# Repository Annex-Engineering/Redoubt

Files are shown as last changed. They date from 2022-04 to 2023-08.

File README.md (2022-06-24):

# Redoubt Printer

> :warning: **This project is still in beta**: Over many months the design has proven itself in the closed beta. However dedicated skirts for the z drives are still missing. Partial CAD is included to make any design as you wish.

Redoubt is entirely scratch design based on the efforts of the V2.2 for better performance, reliability and less maintenance. 

Our discord server can be found here: 

Join me on Discord (https://discord.gg/MzTR3zE)

BOM/Sourcing Guide can be found here: https://docs.google.com/spreadsheets/d/1O3eyVuQ6M4F03MJSDs4Z71_XyNjXL5HFTZr1jsaAtRc/edit?usp=sharing

# Project Goals:
- QuickDraw V2 probe
- Integrated Sherpa Mini
- Ultra compact and anti-backlash swivel z-joints
- Heavy duty XY and Z belt tensioning with one knob
- New CFD optimized part cooling ducts
- Reinforced XY joints
- Optimized for reduced belt wear
- Bearings with improved lifespan
- Quick-swap umbilical
- Carabiner support
- Reduced toolhead weight
- MGN12H support

Note: Enclosed Printers are passively heated and only designed around a 65C max chamber temperature, Redoubt is not intended to be a High Temperature printer. It was designed to excell at common engineering materials such as PLA, PETG, ABS and some PC/Nylon Blends

# Images
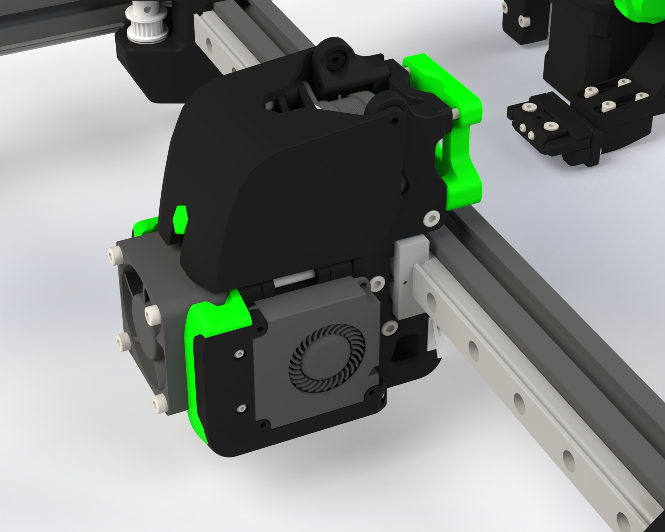
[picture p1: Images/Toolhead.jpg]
Image of Redoubt
 
  
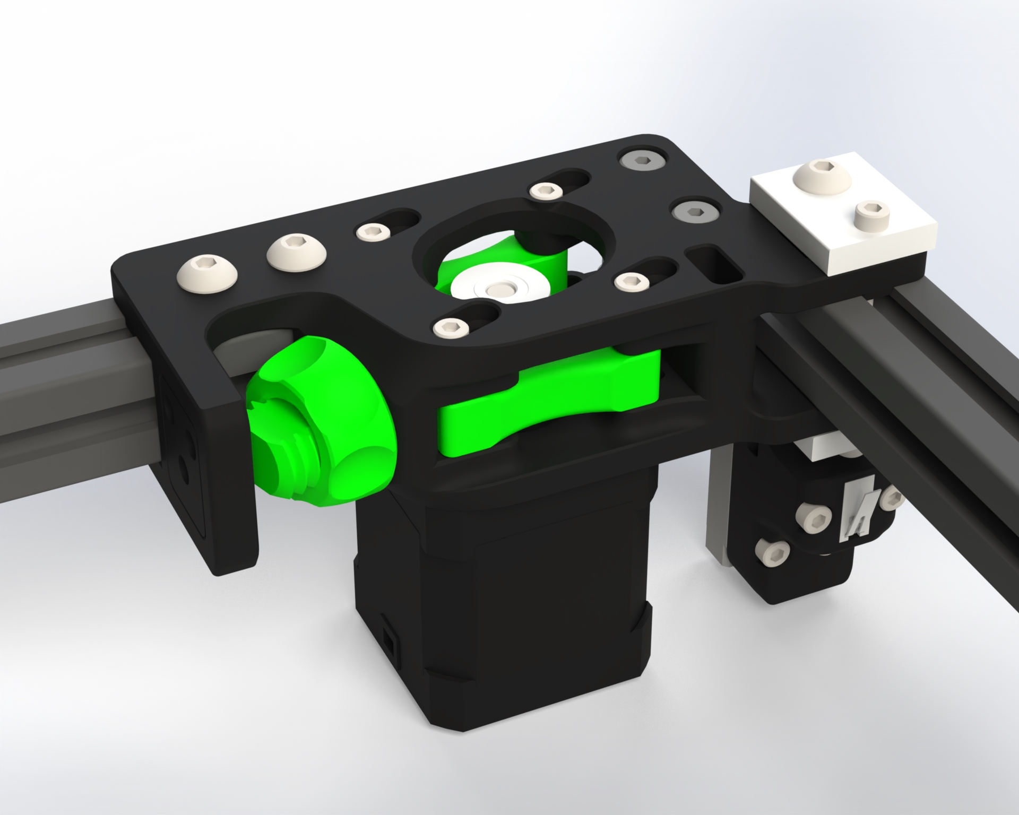
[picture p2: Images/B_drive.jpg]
Image of Redoubt
  

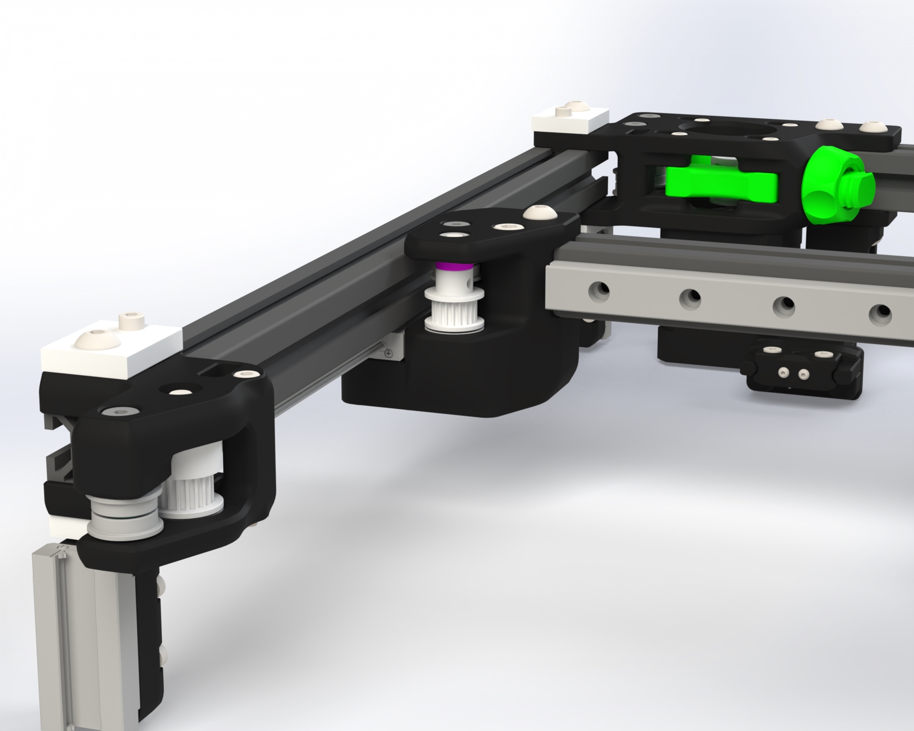
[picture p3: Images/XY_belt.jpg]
Image of Redoubt
 

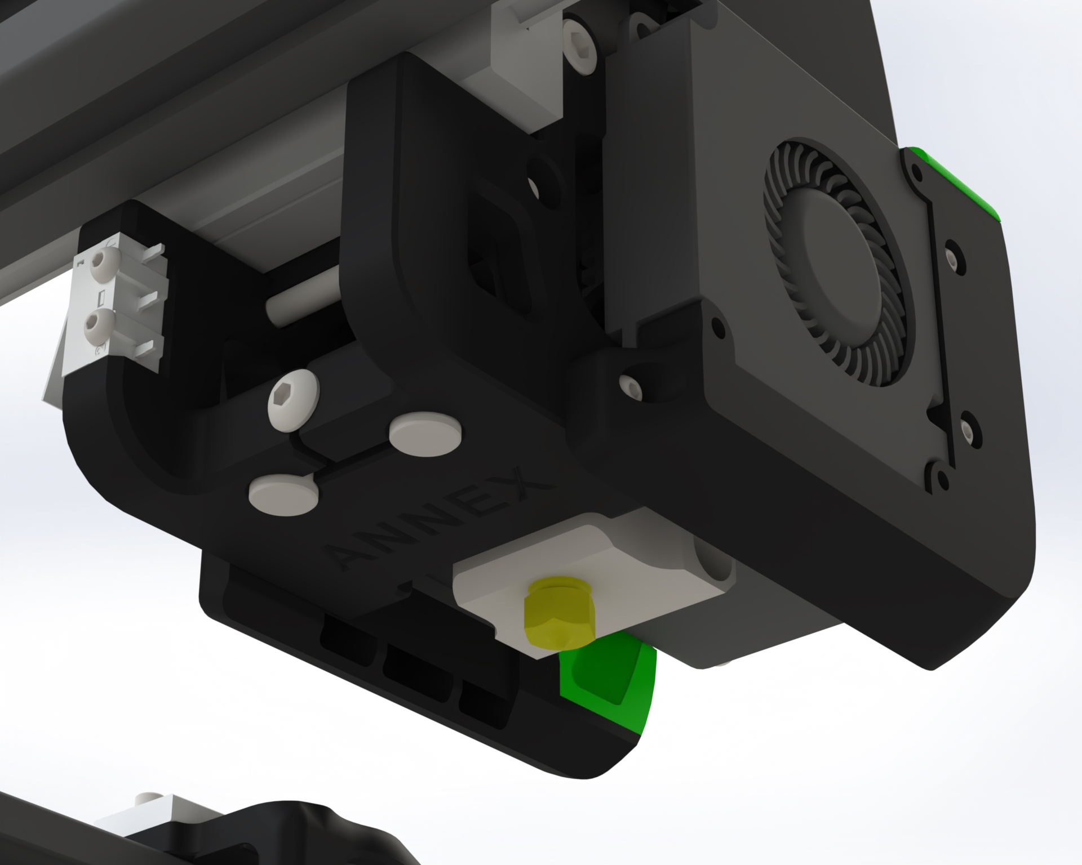
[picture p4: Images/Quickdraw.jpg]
Image of Redoubt
  
 
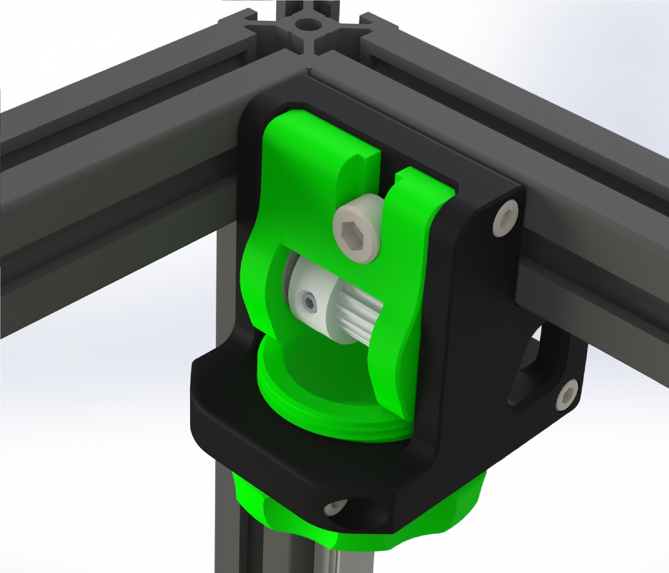
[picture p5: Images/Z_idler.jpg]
Image of Redoubt


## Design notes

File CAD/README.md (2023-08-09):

# Redoubt Printer

The CAD is from the Redoubt_Alpha_Mosquito_25_4_2022.EASM eDrawing with the worm z drives. You are welcome to make any necessary adaptations for different hotends and skirt designs according to your preferences. We would greatly appreciate your feedback and visual contributions on the Annex discord platform.

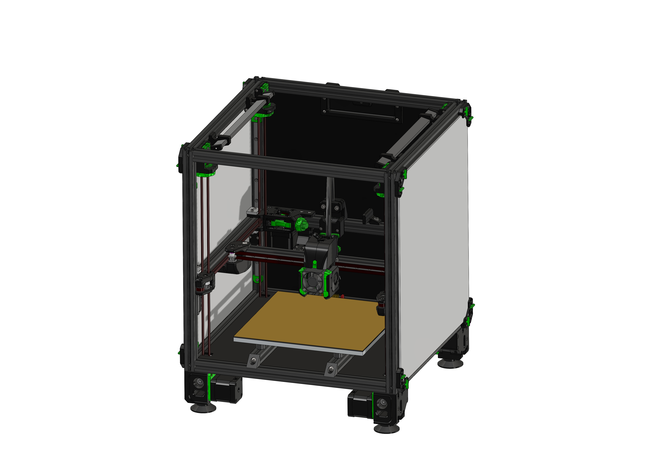
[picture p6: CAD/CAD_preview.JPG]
Image of Redoubt


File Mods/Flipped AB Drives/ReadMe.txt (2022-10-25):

This mod flips the motors on the AB drives so that they face upwards. This is important it you are running a flipped z configuration as it will prevent collisions between your steppers and the z idlers.

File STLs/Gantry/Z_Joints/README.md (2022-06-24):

# Compact swivel z joints

The Y-endstop is now hidden inside one of the z joints. This gives the gantry a cleaner look. Wiring goes behind the nema17 to the z chain. The spacer got new fins that will avoid botteming out the M10 screw and cracking the plastic.

Use 2 M2 self tappers to lock the switch in place. Start with the left side to avoid tilting. The switch can be removed by pushing a small key through the hole on the back.

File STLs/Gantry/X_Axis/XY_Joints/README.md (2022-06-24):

# XY Joints 

No more tall shimstacks are needed. The layout has been optimized for part strength and overtravel in the best way possible. Internal channels are used to reinforce the design. Use locknuts for additional security.

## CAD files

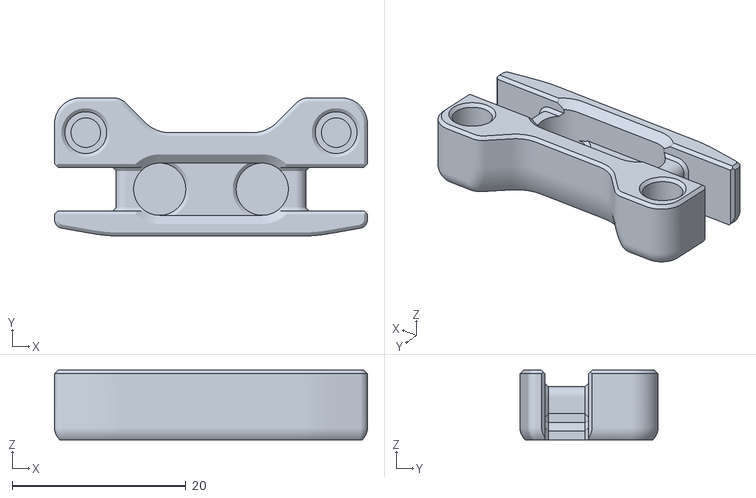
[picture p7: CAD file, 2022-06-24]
STLs/Gantry/QuickDraw V2/Dock_main_x1_Rev3.STL
36.0 x 15.9 x 8.00

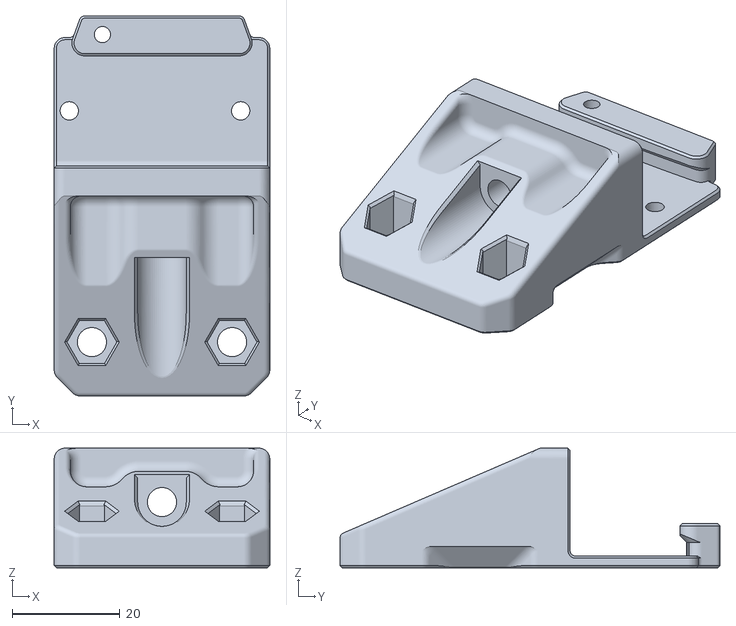
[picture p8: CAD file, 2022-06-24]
STLs/Gantry/Wiring/Cable_clamp_Carabiner_main_x1_Rev1.STL
40.0 x 70.5 x 22.2

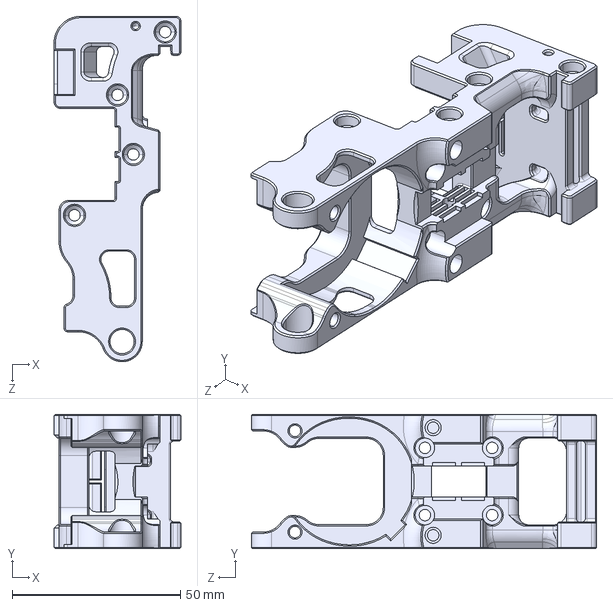
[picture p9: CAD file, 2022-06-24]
CAD/X_carriage.STEP
37.8 x 40.0 x 102.7 mm

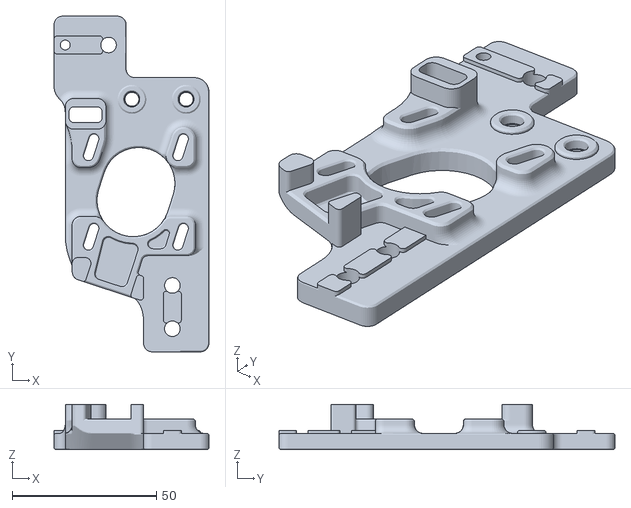
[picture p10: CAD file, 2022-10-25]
Mods/Flipped AB Drives/AB_Drive_bottem_L_Rev8_Flipped.STL
53.7 x 116.3 x 15.6

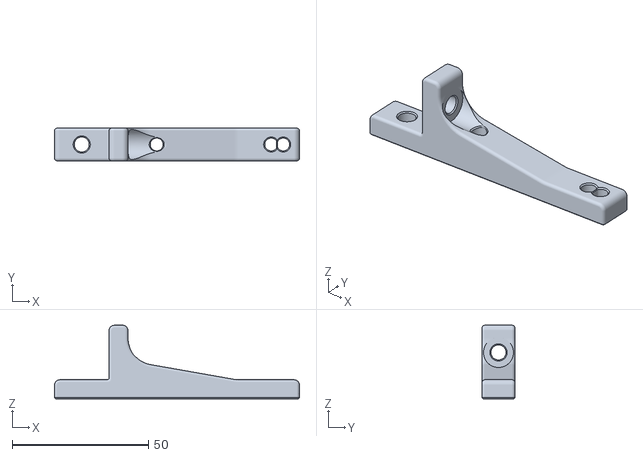
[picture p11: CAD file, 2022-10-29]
STLs/Electronics_Compartment/universal_meanwell_uhp_psu_mounting_bracket_x2_rev2.STL
89.9 x 12.0 x 27.0

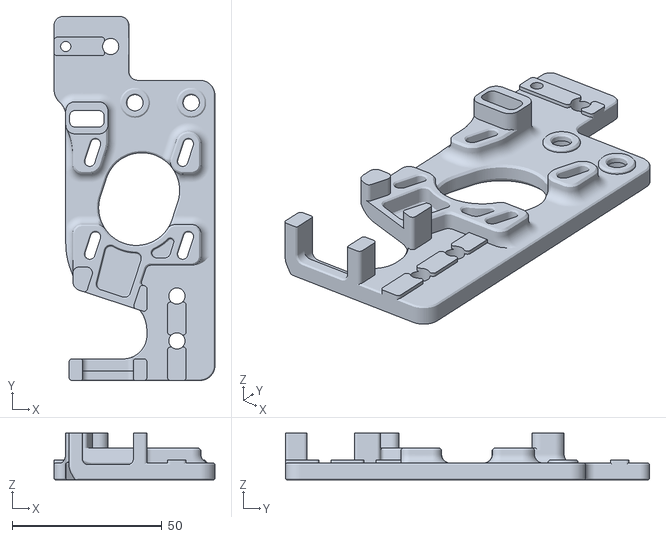
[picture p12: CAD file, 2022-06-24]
STLs/Gantry/AB_Drive_Units/B_Drive_top_ISO7379_x1_Rev4.STL
53.7 x 121.5 x 15.6

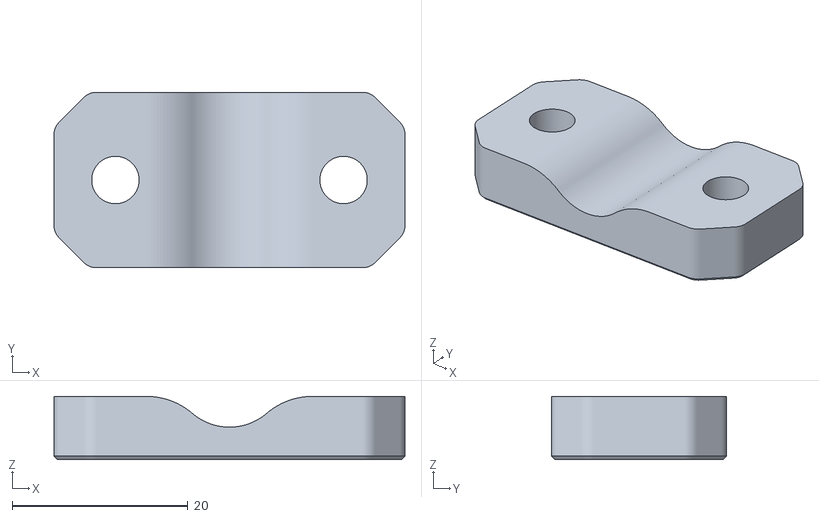
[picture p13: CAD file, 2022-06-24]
STLs/Gantry/Wiring/Cable_clamp_Carabiner_rear_x1_Rev1.STL
40.0 x 20.0 x 7.20

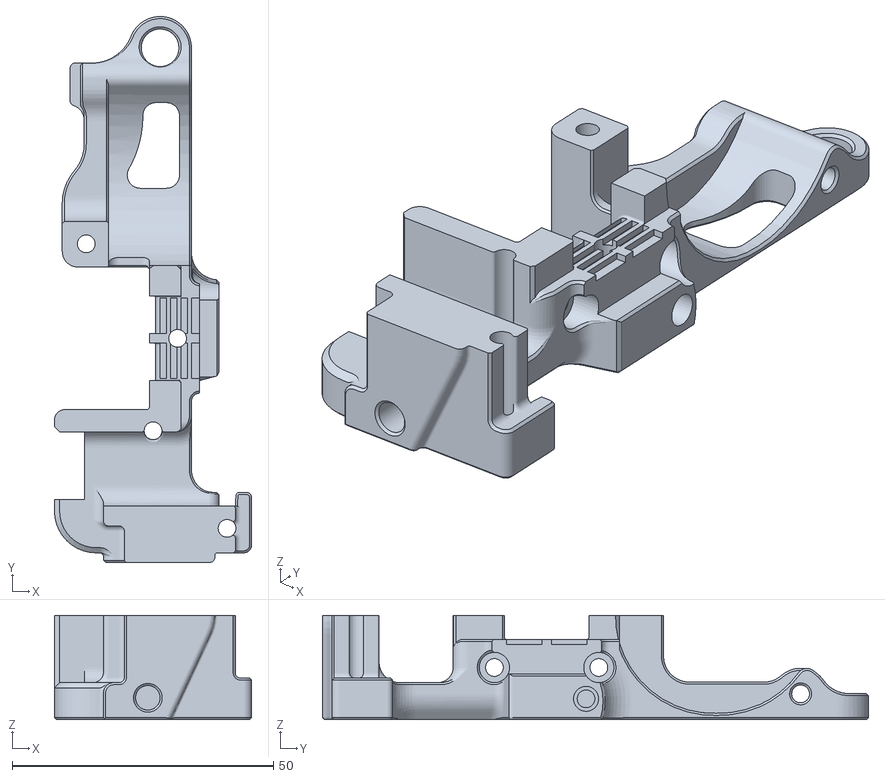
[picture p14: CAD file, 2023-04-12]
STLs/Gantry/X_Axis/X_Carriage/Beacon Carriage/X_carriage_R_Beacon_x1_Rev4.STL
37.8 x 104.6 x 20.0

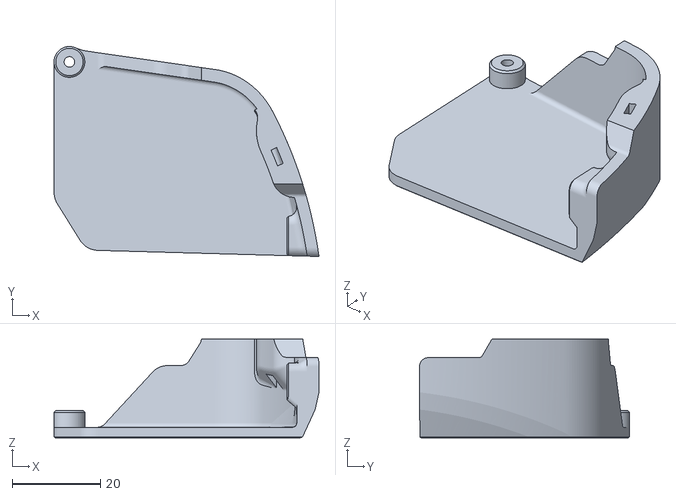
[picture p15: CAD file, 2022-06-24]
STLs/Gantry/X_Axis/X_Carriage/Toolhead_door_right_Rev2_x1.STL
60.1 x 47.6 x 22.4

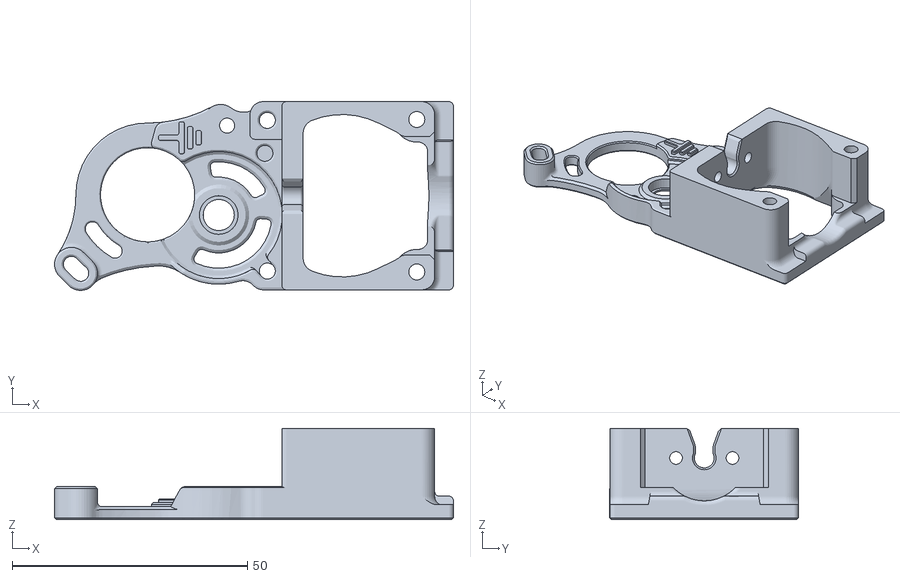
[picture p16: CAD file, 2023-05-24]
STLs/Gantry/X_Axis/X_Carriage/Toolheads/Hotends/Mosquito_hotend_mount_rear_Rev3.STL
84.8 x 40.1 x 19.4

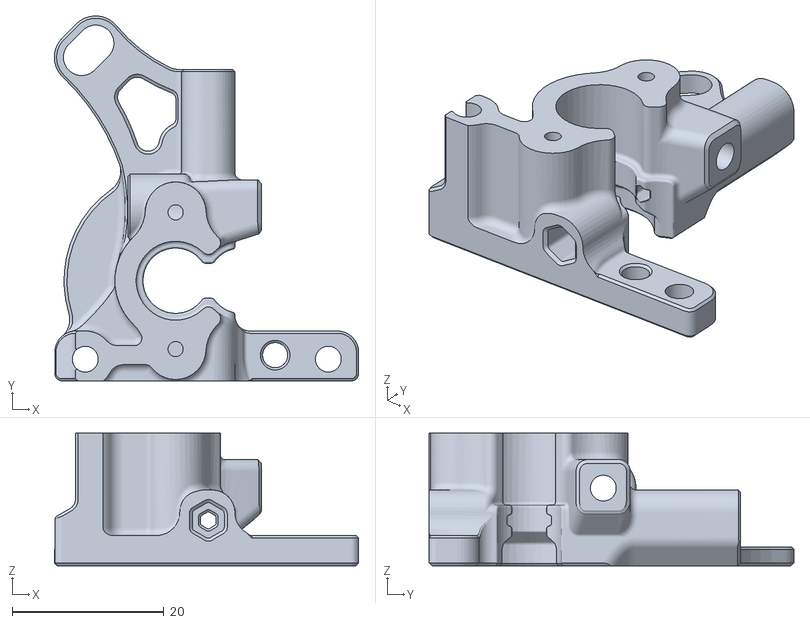
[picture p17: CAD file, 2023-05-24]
STLs/Gantry/X_Axis/X_Carriage/Toolheads/Sherpa_mini_core_x1_rev2.STL
40.1 x 48.0 x 17.5

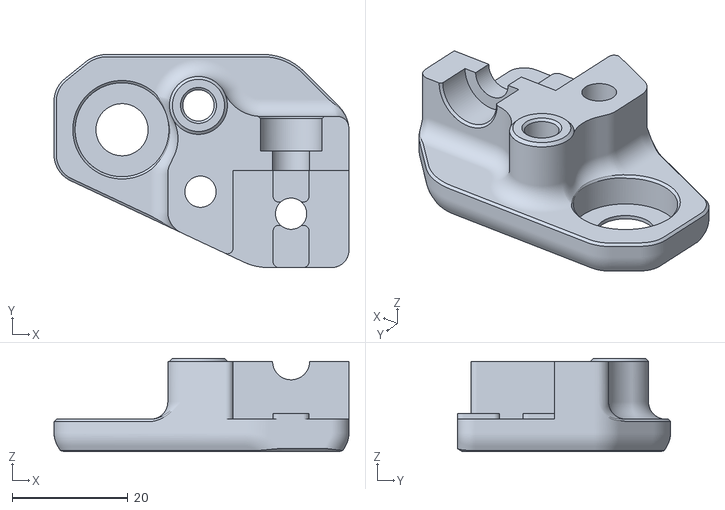
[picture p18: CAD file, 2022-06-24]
STLs/Gantry/X_Axis/XY_Joints/XY_joint_R_top_ISO7979_x1_Rev4.STL
50.9 x 36.8 x 16.1

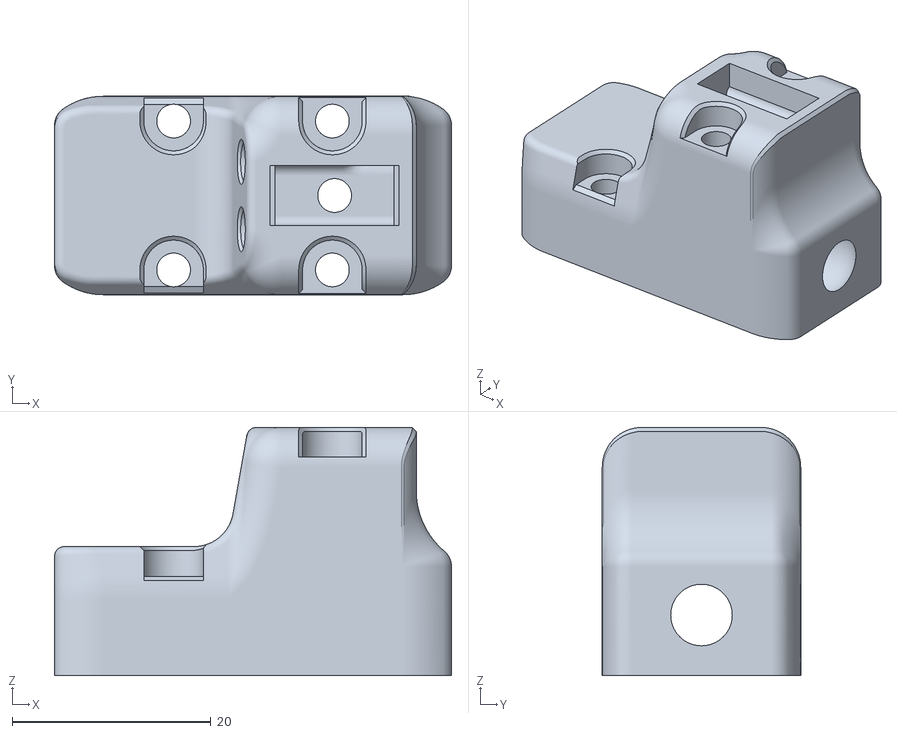
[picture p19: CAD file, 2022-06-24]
STLs/Gantry/Z_Joints/z_bearing_block_x1_Rev4_Y_endstop.STL
40.0 x 20.0 x 25.0

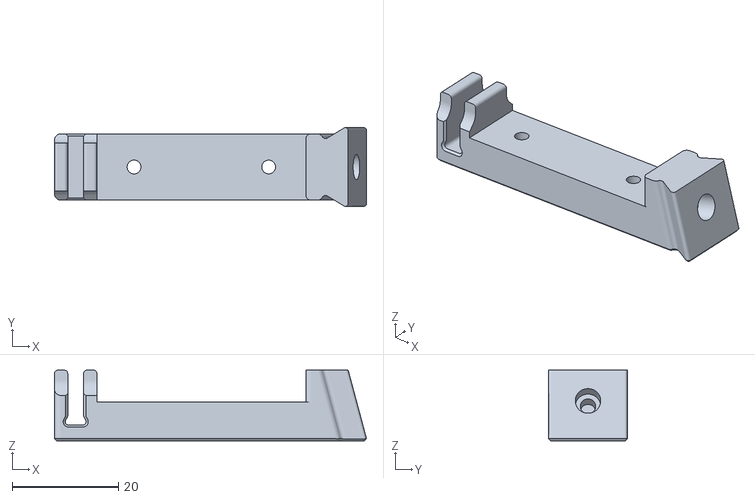
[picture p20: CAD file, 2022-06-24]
STLs/Misc/Brush_wipe_tray/Brush_holder_1x_Rev1.STL
58.8 x 14.8 x 13.3

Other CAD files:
STLs/Misc/LED_2835_bar_mount/LED_Mount_L_2x_Rev1.STL
STLs/Panel_Mounting/Corner/corner_lock_body_9.5.STL
STLs/Panel_Mounting/Exhaust_cover_x1_Rev1.STL
STLs/Panel_Mounting/Key/key_asymmetric_3.5.STL
CAD/Deprecated/X_carriage.x_t
CAD/X_carriage.x_t
Mods/Flipped AB Drives/AB_Drive_bottem_R_Rev8_Flipped.STL
Mods/Flipped AB Drives/AB_Drive_top_L_Rev3_Flipped.STL
Mods/Flipped AB Drives/AB_Drive_top_R_Rev3_Flipped.STL
STLs/Electronics_Compartment/2020_Electronics_Box_Mounting_Bracket_x4_rev1.STL
STLs/Electronics_Compartment/ED24_SSR_mount_x1_rev2.stl
STLs/Electronics_Compartment/[a]_universal_controller_mounting_bracket_b_x2_rev1.STL
STLs/Electronics_Compartment/[a]_universal_rpi_mounting_bracket_b_x2_rev1.STL
STLs/Electronics_Compartment/meanwell_lrs_150_24_psu_mounting_bracket_x2_rev2.STL
STLs/Electronics_Compartment/universal_controller_mounting_bracket_a_x2_rev3.STL
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

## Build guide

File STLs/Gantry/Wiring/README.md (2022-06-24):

# Cable clamp options

The choice between a traditional umbilical or umbilical with carabiner can be made. Use a (printed) spacer when mounting the PCB. Using the carabiner allows quick cable swaps in case of a strand failure due to wear.

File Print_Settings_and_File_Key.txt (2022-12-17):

Primary Color: nothing at start of file name
Accent Color: [a]_ at start of file name
Quantity Required: _x# near end of file name
File Revision: _Rev# at end of file name

Nozzle Size: 0.5mm 
Recommended FDM Materials: ASA, Polymaker or 3DXTech Recommended
Alternate Approved FDM Materials: PC, 3DXTech Recommended
Layer Height: 0.25mm
Extrusion Width: Forced 0.5mm
Infill Percentage: 40% minimum (at 0.8mm Width)
Infill Type: Grid, Gyroid, Honeycomb, Triangle or Cubic
Wall Count: 3 minimum (at 0.5mm Width)
Solid Top/Bottom Layers: 4 minimum (at 0.5mm Height)

Nozzle Size: 0.4mm 
Recommended FDM Materials: ASA, Polymaker or 3DXTech Recommended
Alternate Approved FDM Materials: PC, 3DXTech Recommended
Layer Height: 0.20mm or 0.25mm
Extrusion Width: Forced 0.4mm
Infill Percentage: 40% minimum (at 0.6mm Width)
Infill Type: Grid, Gyroid, Honeycomb, Triangle or Cubic
Wall Count: 4 minimum (at 0.4mm Width)
Solid Top/Bottom Layers: 4 minimum (at 0.25mm Height)

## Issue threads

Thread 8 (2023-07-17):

STEP files for AB_Drive Unit

0xZm1t53r, 2023-07-17:
Hello,

I am thrilled about the concept of having the belt tensioner integrated inside the drive unit. I was wondering if there is a possibility to obtain the STEP files for the AB_Drive unit? I have some modifications in mind that I would like to implement to meet my specific requirements.

Thank you in advance for your assistance.

PapeJelly, 2023-08-23:
Full CAD of current status has been released, this should have all the parts you need.

Closed 2023-08-23.

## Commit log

2021-01-04 add reinforced gantry mounts to repo
    [14.5mm_microswitch_spacer_Rev1.stl, Redoubt Z joints.STEP, Redoubt_z_joints_rev2.x_t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]
2021-01-04 Add support halleffect/microswitch endstop + fix print orientation
    [halleffect_spacer_Rev1.STL, microswitch_spacer_Rev1.STL, z_bearing_block_x4_Rev2.STL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]
2022-04-25 Add images and Readme
    [14.5mm_microswitch_spacer_Rev1.stl, Redoubt Z joints.STEP, Redoubt_z_joints_rev2.x_t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]
2022-06-24 First push open beta
    [2020_Electronics_Box_Mounting_Bracket.STL, 4010_Cooling_Duct_L_x1_rev3.stl, 4010_Cooling_Duct_R_x1_rev3.stl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]
2022-06-24 Update README.md
    use the correct bom link
2022-07-30 fixed duct clearance for dragon hotend mount
    [Dragon_hotend_mount_rear_Rev2.STL, Dragon_hotend_mount_rear_Rev3.STL]
2022-10-25 Mods Folder and flipped AB Mod
    Flipped the AB drive motor side to allow for top mounted z setup without collision.
    [AB_Drive_bottem_L_Rev8_Flipped.STL, AB_Drive_bottem_R_Rev8_Flipped.STL, AB_Drive_top_L_Rev3_Flipped.STL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]
2022-10-29 update ebox brackets to latest revisions
    [ED24_SSR_mount_x1_rev2.stl, WAGO_Mount_5x2_24VDC.STL, WAGO_Mount_5x2_48VDC.STL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]
2022-10-29 rename folder
    [Brush_holder_1x_Rev1.STL, LED_Cap_2x_Rev1.STL, LED_Cap_Cable_2x_Rev1.STL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]
2022-11-28 parts did not have multiple required
    [Clip_dock_x1_Rev2.STL, Dock_main_x1_Rev3.STL, Probe_holder_d2f_x1_rev1.STL]
2022-11-28 more file naming fixes
    [2020_Electronics_Box_Mounting_Bracket_x4_rev1.STL, Z_Idler_Frame_A_L_x2_Rev1.STL, Z_Idler_Frame_A_R_x2_Rev1.STL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]
2022-11-28 more naming convention fixes
    [[a]_Drive_tension_knob_x2_Rev2.STL, [a]_Tensioner_frame_x2_Rev2.STL]
2023-04-02 Beacon Support
    Added beacon support to Redoubt carriage.
    [X_carriage_L_Beacon_x1_Rev4.STL, X_carriage_R_Beacon_x1_Rev4.STL]
2023-05-24 Adjusted slot to allow proper 8t meshing
    [Dragon_hotend_mount_rear_Rev3.STL, Dragon_hotend_mount_rear_Rev4.STL, Mosquito_hotend_mount_rear_Rev2.STL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]
2023-08-09 Add Alpha CAD
    [X_carriage.STEP, X_carriage.x_t]
2023-10-27 migrate printer, extruder and board configs to an MIT licensed repo
